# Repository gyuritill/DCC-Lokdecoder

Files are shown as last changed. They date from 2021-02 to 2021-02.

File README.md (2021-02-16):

# DCC-Lokdecoder
## Description
DCC multifunction decoder for H0 locomotives
## Features
- 1 motor H-bridge output
  - 3.6 A peak current
  - PWM frequency configurable (1-40 kHz)
  - overcurrent and temperature protected
- 10 function outputs
  - 115 mA per output
  - F0f, F0r, AUX1 and AUX2 are dimmable *todo*
  - mappable to F0-F12 function keys
- DCC asymmetry can be detected (for automatic brake control) *todo*
## Hardware
- 4-layer PCB esigned in KiCAD
- fairly standard components (available from Digi-Key, Farnell, Mouser, etc...)
- hand solderable (I did it too)
- 4 debug LEDs (red, yellow, green and blue)

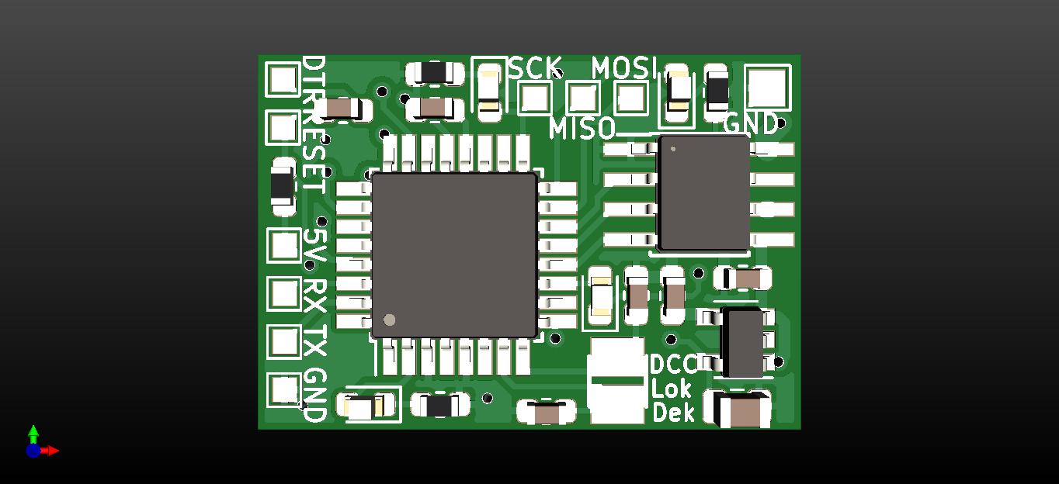
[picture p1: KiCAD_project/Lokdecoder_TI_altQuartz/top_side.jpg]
top
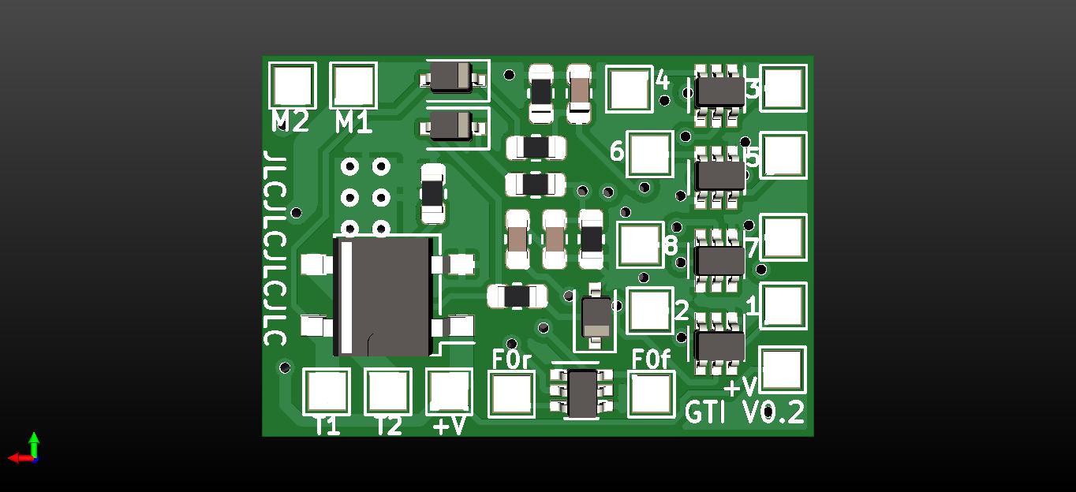
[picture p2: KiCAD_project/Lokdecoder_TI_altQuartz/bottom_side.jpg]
bottom
|  |  |
| :---: | :---: |
| top side | bottom side |

## Firmware
- Arduino compatible programming (behaves like an UNO)
- DCC decoding by [NmraDcc](https://github.com/mrrwa/NmraDcc) library

## JMRI integration

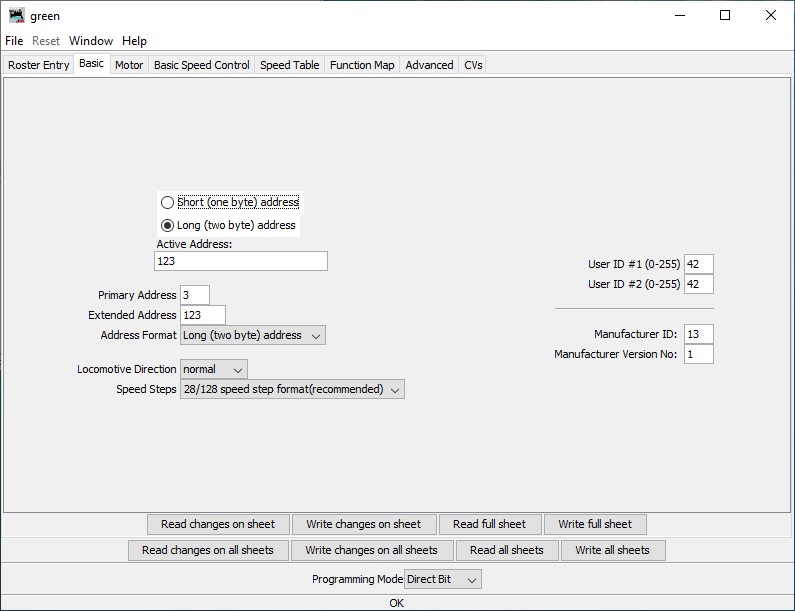
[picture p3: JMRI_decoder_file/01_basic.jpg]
basic
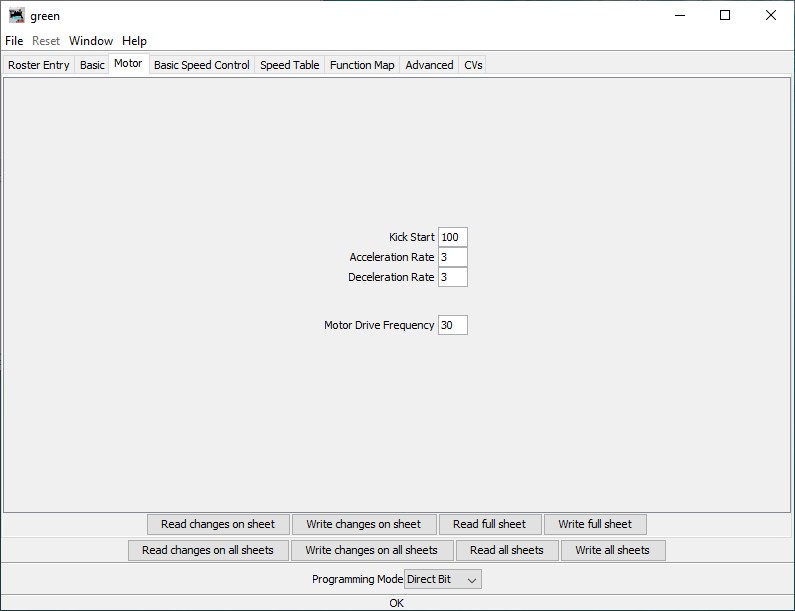
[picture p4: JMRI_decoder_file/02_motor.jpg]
motor
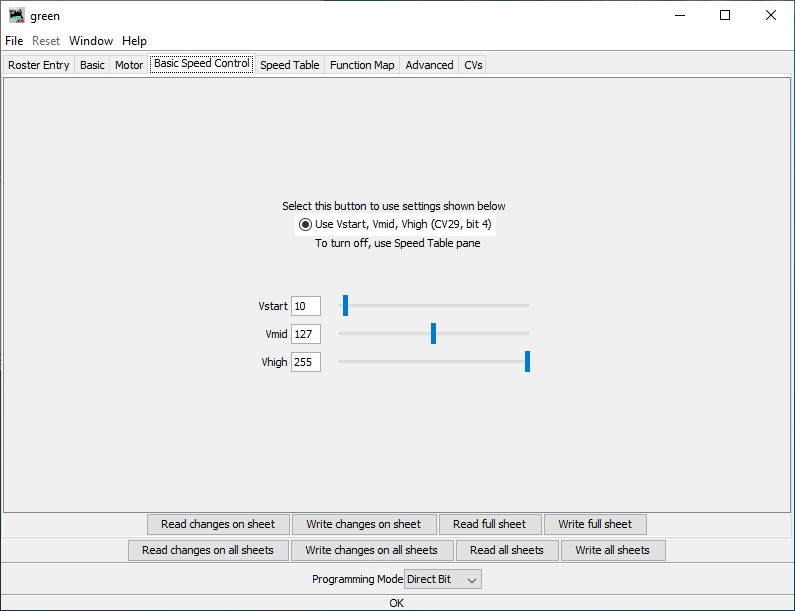
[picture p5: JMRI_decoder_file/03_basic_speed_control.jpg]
basic_speed
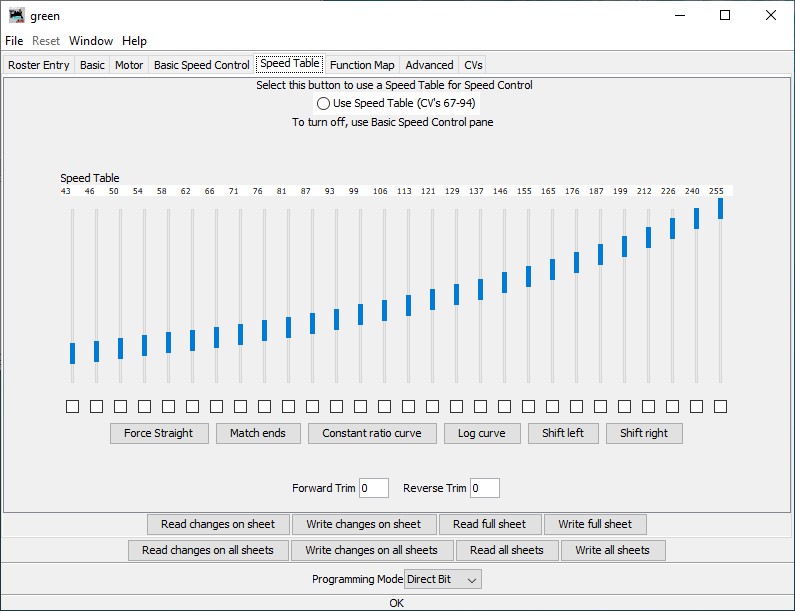
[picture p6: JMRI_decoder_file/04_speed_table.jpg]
speed_table
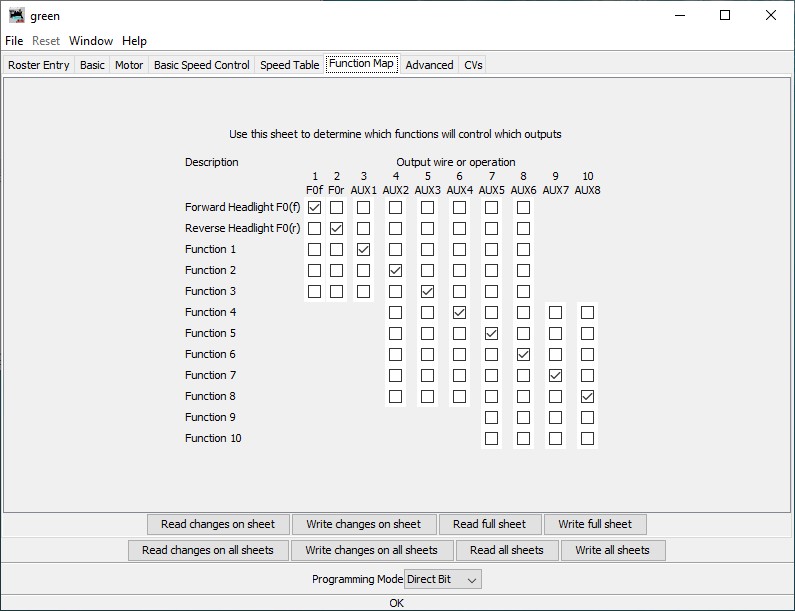
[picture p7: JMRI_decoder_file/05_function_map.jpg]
function_map
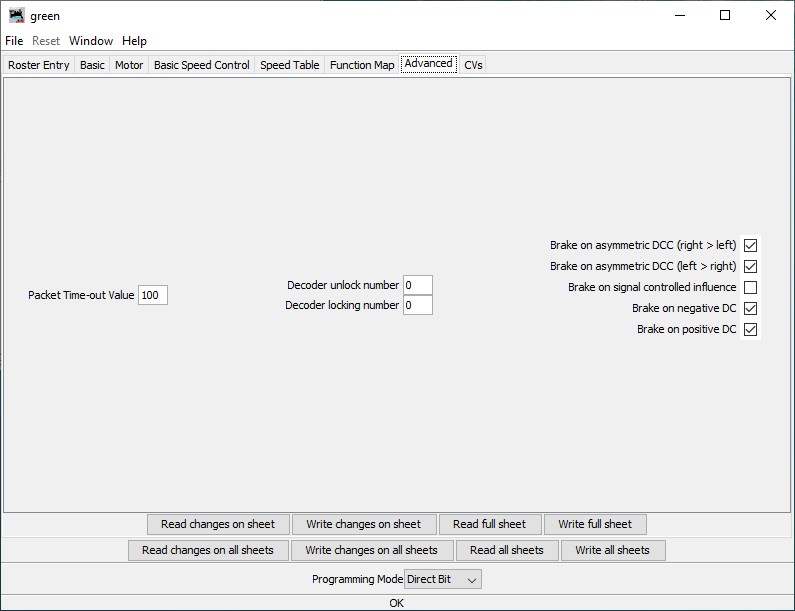
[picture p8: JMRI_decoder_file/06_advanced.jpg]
advanced
|  |  |  |  |  |  |
| :---: | :---: | :---: | :---: | :---: | :---: |
| Basic  | Motor | Basic speed control | Speed table | Function map | Advanced |

## Install guide

1. Get the PCB (e.g. [JLCPCB](https://jlcpcb.com/)) and the components (e.g. [mouser](https://www.mouser.at/), [digikey](https://www.digikey.at/))
2. Solder the components. The SOIC with exposed pad is a bit tricky, it can be soldered from the other side with a big tip and a lot of flux.
3. Install the Arduino bootloader using the pads 5V, GND, SCK, MISO, MOSI, RST and an Arduino. [Arduino as ISP](https://www.arduino.cc/en/Tutorial/BuiltInExamples/ArduinoISP)
4. Uncomment the line `#define RESET_FACTORY_DEFAULTS` to fill the EEPROM with the default CV values
5. Upload the code using the pads 5V, GND, RX, TX, DTR and a USB TTL UART cable [like this](https://www.mouser.at/ProductDetail/FTDI/TTL-232R-5V-WE/?qs=OMDV80DKjRpCUAS6UR9QpQ%3D%3D)
6. Re-comment the line `#define RESET_FACTORY_DEFAULTS` to avoid resetting to factory defaults every time.
7. Upload the code again.
8. Add the decoder XML file to JMRI. In DecoderPro select "File-> Import Decoder File..." and browse to the decoder [XML](JMRI_decoder_file/Public_Domain_GTI_green.xml). It will take some time, then adds the decoder definition to the database.
9. Connect the T1 and T2 pads to the programming track of your DCC system.
10. Add new locomotive with the "New Loco" button and then "Read type from decoder". It should detect the correct type:
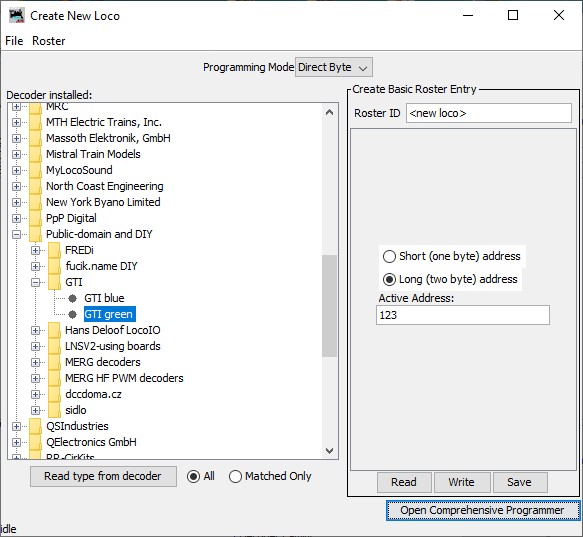
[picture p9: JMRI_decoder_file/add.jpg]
add

11. If everything is fine, you can install the decoder into your locomotive!
### Pinout
| Pad | Function |
| :-- | :-- |
| M1 | Motor 1 |
| M2 | Motor 2 |
| T1 | Track 1 |
| T2 | Track 2 |
| V+ | Positive common for function outputs (keep-alive capacitor positive) |
| F0f | F0 function output forward (open drain) |
| F0r | F0 function output reverse (open drain) |
| 1-8 | AUX function output n (open drain) |
| 5V | internal microcontroller +5V supply |
| GND | ground (keep alive capacitor negative) |
| SCK | ISP programming clock (connect to ISP SCK) |
| MISO | ISP programming read (connect to ISP MISO) |
| MOSI | ISP programming write (connect to ISP MOSI) |
| RST | ISP programming reset (connect to ISP reset output)
| RX | serial programming receive (connect to TTL UART TX) |
| TX | serial programming transmit (connect to TTL UART RX) |
| DTR | serial programming reset through a 100 nF capacitor (connect to TTL UART DTR) |

## Todo list
- [ ] CV15, CV16 decoder locking
- [ ] CV65 kick start
- [ ] CV67-94 speed table
- [ ] CV27 automatic brake control
- [ ] function output dimming
- [ ] motor fault check

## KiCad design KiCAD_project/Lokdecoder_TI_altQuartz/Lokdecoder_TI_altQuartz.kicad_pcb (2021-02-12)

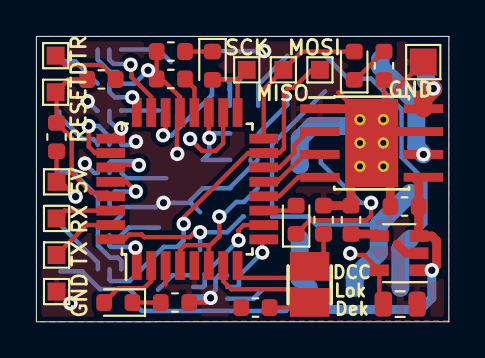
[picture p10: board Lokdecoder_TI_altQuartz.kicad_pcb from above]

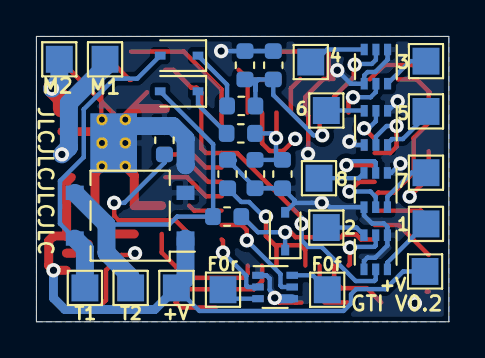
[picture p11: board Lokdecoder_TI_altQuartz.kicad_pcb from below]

Board: 4 copper layers, 22.9 x 15.8 mm, 63 parts (34 on the bottom side), 51 nets.

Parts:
C1, C2, C5, C10: 100nF; C_0603_1608Metric
C3: 470pF; C_0603_1608Metric
C4: 2.2uF; C_0805_2012Metric
C6, C7: 4.7uF; C_0603_1608Metric
C8, C9: 10pF; C_0603_1608Metric
D1: D_Bridge_+-AA; TO-269AA
D2: MM3Z4V7ST1G; D_SOD-323
D3, D4: NSR0530HT1G; D_SOD-323
D5: Ye_LED; LED_0603_1608Metric
D6: Gr_LED; LED_0603_1608Metric
D7: Rd_LED; LED_0603_1608Metric
D8: Bl_LED; LED_0603_1608Metric
IC1: MIC5205-5.0YM5-TR; SOT-23-5
IC2: ATMEGA328P-AUR; TQFP-32_7x7mm_P0.8mm
IC3: DRV8872DDAR; Texas_HTSOP-8-1EP_3.9x4.9mm_P1.27mm_EP2.95x4.9mm_Mask2.4x3.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
R1, R5, R6: 4.7k; R_0603_1608Metric
R2, R3, R4: 27k; R_0603_1608Metric
R7, R9, R10, R11: 1k; R_0603_1608Metric
T1, T2, T3, T4, T5: 2N7002DWCT; SOT-363_SC-70-6
TP1: M1; TestPoint_Pad_1.5x1.5mm
TP2: M2; TestPoint_Pad_1.5x1.5mm
TP3: T1; TestPoint_Pad_1.5x1.5mm
TP4: T2; TestPoint_Pad_1.5x1.5mm
TP5: GND; TestPoint_Pad_1.5x1.5mm
TP6, TP17: +V; TestPoint_Pad_1.5x1.5mm
TP7: F0f; TestPoint_Pad_1.5x1.5mm
TP8: F0r; TestPoint_Pad_1.5x1.5mm
TP9: 1; TestPoint_Pad_1.5x1.5mm
TP10: 2; TestPoint_Pad_1.5x1.5mm
TP11: 3; TestPoint_Pad_1.5x1.5mm
TP12: 4; TestPoint_Pad_1.5x1.5mm
TP13: 5; TestPoint_Pad_1.5x1.5mm
TP14: 6; TestPoint_Pad_1.5x1.5mm
TP15: 7; TestPoint_Pad_1.5x1.5mm
TP16: 8; TestPoint_Pad_1.5x1.5mm
TP18: RESET; TestPoint_Pad_1.0x1.0mm
TP19: SCK; TestPoint_Pad_1.0x1.0mm
TP20: MISO; TestPoint_Pad_1.0x1.0mm
TP21: MOSI; TestPoint_Pad_1.0x1.0mm
TP22: 5V; TestPoint_Pad_1.0x1.0mm
TP23: RX; TestPoint_Pad_1.0x1.0mm
TP24: TX; TestPoint_Pad_1.0x1.0mm
TP25: DTR; TestPoint_Pad_1.0x1.0mm
TP26: GND; TestPoint_Pad_1.0x1.0mm
X1: 16M; Crystal_SMD_2520-2Pin_2.5x2.0mm_HandSoldering

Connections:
+5V: C4.1, C5.2, IC1.5, IC2.4, IC2.6, IC2.18, R1.2, TP22.1
/A0: IC2.23, T4.2
/A1: IC2.24, T4.5
/A2: IC2.25, T5.2
/A3: IC2.26, T5.5
/A4: IC2.27, T3.2
/A5: IC2.28, T3.5
/A6: C6.2, IC2.19, R3.1, R5.1
/A7: C7.2, IC2.22, R4.1, R6.1
/AUX1: T2.6, TP9.1
/AUX1_TTL: IC2.1, T2.2
/AUX2: T2.3, TP10.1
/AUX2_TTL: IC2.15, T2.5, TP21.1
/AUX3: T4.6, TP11.1
/AUX4: T4.3, TP12.1
/AUX5: T5.6, TP13.1
/AUX6: T5.3, TP14.1
/AUX7: T3.6, TP15.1
/AUX8: T3.3, TP16.1
/D0: IC2.30, TP23.1
/D1: IC2.31, TP24.1
/D2: D2.1, IC2.32, R2.1
/D4: D8.2, IC2.2
/D5: IC2.9, T1.2
/D6: IC2.10, T1.5
/D7: D7.2, IC2.11
/D8: IC2.12, IC3.4
/D9: IC2.13, IC3.3
/D10: IC2.14, IC3.2
/D12: D6.2, IC2.16, TP20.1
/D13: D5.2, IC2.17, TP19.1
/DCC1: D1.4, D4.2, TP3.1
/DCC2: D1.3, D3.2, R2.2, TP4.1
/DTR: C1.2, TP25.1
/F0f: T1.6, TP7.1
/F0r: T1.3, TP8.1
/MOT1: IC3.6, TP1.1
/MOT2: IC3.8, TP2.1
/RESET: C1.1, IC2.29, R1.1, TP18.1
GND: C2.2, C3.1, C4.2, C5.1, C6.1, C7.1, C8.1, C9.1, C10.1, D1.2, D2.2, IC1.2, IC2.3, IC2.5, IC2.21, IC3.1, IC3.7, IC3.9, R5.2, R6.2, R7.1, R9.1, R10.1, R11.1, T1.1, T1.4, T2.1, T2.4, T3.1, T3.4, T4.1, T4.4, T5.1, T5.4, TP5.1, TP26.1
unnamed: C2.1, IC2.20
unnamed: C3.2, IC1.4
unnamed: C8.2, IC2.7, X1.1
unnamed: C9.2, IC2.8, X1.2
unnamed: D3.1, R3.2
unnamed: D4.1, R4.2
unnamed: D5.1, R9.2
unnamed: D6.1, R10.2
unnamed: D7.1, R11.2
unnamed: D8.1, R7.2
VCC: C10.2, D1.1, IC1.1, IC1.3, IC3.5, TP6.1, TP17.1

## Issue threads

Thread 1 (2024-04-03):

Questions about setting a high PWM frequency and motor drive handling

murarduino, 2024-04-03:
Dear gyuritill,

I noticed that in your project, the motor driver component is selected from the Ti company DRV8872. This is a typical SOP-8 motor driver chip. I checked the datasheet for DRV8872. In the Fpwm Recommended Operating Conditions has a line in the note:
The voltages applied to the inputs should have at least 800 ns of pulse width to ensure detection. Typical devices require at least 400 ns. If the PWM frequency is 200 kHz, the usable duty cycle range is 16% to 84%

I think this is because it has to do with the motor drive internal MOSFET switching time and the time spent in logic processing. Although only the tDEAD time is listed in the Electrical Characteristics table, this issue is described in 7.3.4 Dead Time.

I understand that this is the minimum duration of a PWM square wave (high level). or that PWM square wave need to be greater than (at least equal to) this time.

In the decoder, the PWM resolution is usually set to 2^8. 256。 The minimum duty cycle needs to be greater than this time
Take the decoder PWM frequency set to 40KHz for example. The PWM cycle time is 25us, and dividing by 256 (1/256) is almost 100ns. According to the note, it is necessary to set the duty cycle to 8 in Vstart (to be equal to 8 in step1 of the Speed Table). Am I right to interpret it this way?
Similarly, in high frequency PWM settings, special attention needs to be paid to the duty cycle value of step1.

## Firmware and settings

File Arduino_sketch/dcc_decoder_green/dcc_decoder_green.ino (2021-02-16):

// for ATMEGA328P
#include <NmraDcc.h>

// Uncomment to force CV Reset to Factory Defaults
//#define RESET_FACTORY_DEFAULTS

// Uncomment any of the lines below to enable debug messages for different parts of the code
//#define DEBUG_DCC_MSG

#if defined(DEBUG_FUNCTIONS) or defined(DEBUG_SPEED) or defined(DEBUG_PWM) or defined(DEBUG_DCC_ACK) or defined(DEBUG_DCC_MSG) or defined(DEBUG_STATE)
#define DEBUG_PRINT
#endif

#define DECODER_ADDRESS 3
#define LONG_ADDRESS 123

#define CV_VSTART 2
#define START_VOLTAGE 10 // 255 is full rectified voltage

#define CV_ACC_RATE 3
#define ACC_RATE 3 // value*0.896/speed_steps sec/step 3->2.688 sec to full speed

#define CV_DEC_RATE 4
#define DEC_RATE 3 // value*0.896/speed_steps sec/step 3->2.688 sec from full speed

#define CV_VHIGH 5
#define HIGH_VOLTAGE 255 // 255 is full rectified voltage

#define CV_VMID 6
#define MID_VOLTAGE 127 // 255 is full rectified voltage

#define VERSION 1           // CV 7

#define CV_PWM_PERIOD 9
#define PWM_PERIOD 1

#define CV_PACKET_TIMEOUT 11
#define PACKET_TIMEOUT 100 // x 10ms
#define CV_UNLOCK_NUMBER 15
#define CV_LOCKING_NUMBER 16
#define CV_AUTO_STOP_CONFIG 27
#define CV_OUTPUT_LOCATION_F0f 33
#define CV_OUTPUT_LOCATION_F0r 34
#define CV_OUTPUT_LOCATION_F1 35
#define CV_OUTPUT_LOCATION_F2 36
#define CV_OUTPUT_LOCATION_F3 37
#define CV_OUTPUT_LOCATION_F4 38
#define CV_OUTPUT_LOCATION_F5 39
#define CV_OUTPUT_LOCATION_F6 40
#define CV_OUTPUT_LOCATION_F7 41
#define CV_OUTPUT_LOCATION_F8 42
#define CV_OUTPUT_LOCATION_F9 43
#define CV_OUTPUT_LOCATION_F10 44
#define CV_OUTPUT_LOCATION_F11 45
#define CV_OUTPUT_LOCATION_F12 46
#define CV_PRODUCT_ID 47  //Product ID: 47-50 (CV47<<24 + CV48<<16 + CV49<<8 + CV50)
#define CV_KICK_START 65
#define CV_FWD_TRIM 66
#define CV_SPEED_MAP 67 //67-94
#define CV_REV_TRIM 95
#define CV_USER_ID1 105
#define CV_USER_ID2 106

//todo
// function effects 57-61, dimming, inverting, 0-speed activate/deactivate
// SW_IN function mapping, minimum time
// overload amplitude, time

#define DCC_PIN       2
#define MOTOR_IN1_PIN 9
#define MOTOR_IN2_PIN 10
#define MOTOR_nFAULT_PIN 8
#define LED_F0f_PIN   5
#define LED_F0r_PIN   6
#define LED_AUX1_PIN  3
#define LED_AUX2_PIN  11
#define LED_AUX3_PIN  A0
#define LED_AUX4_PIN  A1
#define LED_AUX5_PIN  A2
#define LED_AUX6_PIN  A3
#define LED_AUX7_PIN  A4
#define LED_AUX8_PIN  A5
#define LED_GREEN_PIN 12
#define LED_YELLOW_PIN 13
#define LED_RED_PIN    7
#define LED_BLUE_PIN   4
#define DCC1_PK_PIN   A6
#define DCC2_PK_PIN   A7

NmraDcc dcc;

struct CVPair{
  uint16_t CV;
  uint8_t  Value;
};

CVPair factoryDefaultCVs [] =
{
  {CV_MULTIFUNCTION_PRIMARY_ADDRESS, DECODER_ADDRESS&0x7F },//CV1
  {CV_VSTART, START_VOLTAGE },//CV2
  {CV_ACC_RATE, ACC_RATE },//CV3
  {CV_DEC_RATE, DEC_RATE },//CV4
  {CV_VHIGH, HIGH_VOLTAGE },//CV5
  {CV_VMID, MID_VOLTAGE },//CV6, (CV7, CV8 implicit in dcc.init())
  {CV_PWM_PERIOD, PWM_PERIOD},//CV9
  {CV_PACKET_TIMEOUT, PACKET_TIMEOUT},//CV11
  {CV_UNLOCK_NUMBER, 0},//CV15
  {CV_LOCKING_NUMBER, 0},//CV16
  {CV_MULTIFUNCTION_EXTENDED_ADDRESS_MSB, highByte(LONG_ADDRESS) + 0xC0}, //CV17
  {CV_MULTIFUNCTION_EXTENDED_ADDRESS_LSB, lowByte(LONG_ADDRESS)},         //CV18
  {CV_AUTO_STOP_CONFIG, 0b00110011},//CV27 7,6: reserved, 5: DC+, 4: DC-, 3: unused, 2: Signal, 1: Asym left, 0: Asym right
  {CV_29_CONFIG, 0x00
  //| CV29_LOCO_DIR            // 0: normal direction, 1: reversed direction
  | CV29_F0_LOCATION           // 0: 14 speed steps, 1:28/128 speed steps
  //| CV29_APS                 // 0: only DCC, 1: analogue enabled
  //| CV29_ADV_ACK             // 0: Railcom disabled, 1: Railcom enabled
  //| CV29_SPEED_TABLE_ENABLE  // 0: simple speed curve (CV2, CV5, CV6)
#ifdef LONG_ADDRESS
  | CV29_EXT_ADDRESSING        // 0: one byte addressing, 1: two byte addressing
#endif
  //| CV29_OUTPUT_ADDRESS_MODE // 0: Decoder Address Mode, 1: Output Address Mode
  //| CV29_ACCESSORY_DECODER   // 0: Multi-Function Decoder Mode, 1: Accessory Decoder Mode
  },
  //CVs33-46
  {CV_OUTPUT_LOCATION_F0f, 1},// 1:F0f, 2:F0r, 4:AUX1, 8:AUX2, 16:AUX3, 32:AUX4, 64:AUX5, 128:AUX6
  {CV_OUTPUT_LOCATION_F0r, 2},// 1:F0f, 2:F0r, 4:AUX1, 8:AUX2, 16:AUX3, 32:AUX4, 64:AUX5, 128:AUX6
  {CV_OUTPUT_LOCATION_F1, 4}, // 1:F0f, 2:F0r, 4:AUX1, 8:AUX2, 16:AUX3, 32:AUX4, 64:AUX5, 128:AUX6
  {CV_OUTPUT_LOCATION_F2, 8}, // 1:F0f, 2:F0r, 4:AUX1, 8:AUX2, 16:AUX3, 32:AUX4, 64:AUX5, 128:AUX6
  {CV_OUTPUT_LOCATION_F3, 16},// 1:F0f, 2:F0r, 4:AUX1, 8:AUX2, 16:AUX3, 32:AUX4, 64:AUX5, 128:AUX6
  {CV_OUTPUT_LOCATION_F4, 4}, // 1:AUX2, 2:AUX3, 4:AUX4, 8:AUX5, 16:AUX6, 32:AUX7, 64:AUX8
  {CV_OUTPUT_LOCATION_F5, 8}, // 1:AUX2, 2:AUX3, 4:AUX4, 8:AUX5, 16:AUX6, 32:AUX7, 64:AUX8
  {CV_OUTPUT_LOCATION_F6, 16},// 1:AUX2, 2:AUX3, 4:AUX4, 8:AUX5, 16:AUX6, 32:AUX7, 64:AUX8
  {CV_OUTPUT_LOCATION_F7, 32},// 1:AUX2, 2:AUX3, 4:AUX4, 8:AUX5, 16:AUX6, 32:AUX7, 64:AUX8
  {CV_OUTPUT_LOCATION_F8, 64},// 1:AUX2, 2:AUX3, 4:AUX4, 8:AUX5, 16:AUX6, 32:AUX7, 64:AUX8
  {CV_OUTPUT_LOCATION_F9, 0}, // 1:AUX5, 2:AUX6, 4:AUX7, 8:AUX8
  {CV_OUTPUT_LOCATION_F10, 0},// 1:AUX5, 2:AUX6, 4:AUX7, 8:AUX8
  {CV_OUTPUT_LOCATION_F11, 0},// 1:AUX5, 2:AUX6, 4:AUX7, 8:AUX8
  {CV_OUTPUT_LOCATION_F12, 0},// 1:AUX5, 2:AUX6, 4:AUX7, 8:AUX8
  {CV_PRODUCT_ID+0, 0},  // CV47 product ID highest byte
  {CV_PRODUCT_ID+1, 0},  // CV48 product ID high byte
  {CV_PRODUCT_ID+2, 1},  // CV49 product ID low byte
  {CV_PRODUCT_ID+3, 2},  // CV50 product ID lowest byte
  {CV_KICK_START, 100},  // CV65
  {CV_FWD_TRIM, 128},    // CV66
  //CVs 67-94
  {CV_SPEED_MAP+0, 43},
  {CV_SPEED_MAP+1, 46},
  {CV_SPEED_MAP+2, 50},
  {CV_SPEED_MAP+3, 54},
  {CV_SPEED_MAP+4, 58},
  {CV_SPEED_MAP+5, 62},
  {CV_SPEED_MAP+6, 66},
  {CV_SPEED_MAP+7, 71},
  {CV_SPEED_MAP+8, 76},
  {CV_SPEED_MAP+9, 81},
  {CV_SPEED_MAP+10, 87},
  {CV_SPEED_MAP+11, 93},
  {CV_SPEED_MAP+12, 99},
  {CV_SPEED_MAP+13, 106},
  {CV_SPEED_MAP+14, 113},
  {CV_SPEED_MAP+15, 121},
  {CV_SPEED_MAP+16, 129},
  {CV_SPEED_MAP+17, 137},
  {CV_SPEED_MAP+18, 146},
  {CV_SPEED_MAP+19, 155},
  {CV_SPEED_MAP+20, 165},
  {CV_SPEED_MAP+21, 176},
  {CV_SPEED_MAP+22, 187},
  {CV_SPEED_MAP+23, 199},
  {CV_SPEED_MAP+24, 212},
  {CV_SPEED_MAP+25, 226},
  {CV_SPEED_MAP+26, 240},
  {CV_SPEED_MAP+27, 255},
  {CV_REV_TRIM, 128}, //CV95
  {CV_USER_ID1, 42},  //CV105
  {CV_USER_ID2, 42},  //CV106
};

uint8_t factoryDefaultCVIndex = 0;
// state variables
uint8_t numSpeedSteps = SPEED_STEP_128;
uint32_t lastFunctionState;
uint32_t newFunctionState;
uint16_t lastOutputState = 0;
uint16_t newOutputState = 0;
bool lastDirection;   // DCC_DIR_FWD(1): (a+/b-), DCC_DIR_REV(0): rev (a-/b+)
bool newDirection;    // DCC_DIR_FWD(1): (a+/b-), DCC_DIR_REV(0): rev (a-/b+)
bool actualDirection; // DCC_DIR_FWD(1): (a+/b-), DCC_DIR_REV(0): rev (a-/b+)
uint8_t lastSpeed;    // 0-127, 0:EMCY stop, 1: normal stop, 2-127: drive
uint8_t newSpeed;     // 0-127, 0:EMCY stop, 1: normal stop, 2-127: drive
uint8_t actualSpeed;
uint8_t targetSpeed;
uint8_t savedSpeed;
// timing for acceleration / deceleration
uint32_t lastSpeedStep = 0;
uint32_t newSpeedStep = 0;
// timeout
uint32_t packetTimeout;
uint32_t lastPacket;
// configuration variables
uint8_t vStart;
uint8_t vMid;
uint8_t vHigh;
uint8_t accRate;
uint8_t decRate;
uint8_t pwmFreq;
uint8_t fwdTrim;
uint8_t revTrim;
uint8_t kickStart;
uint8_t functionMapping[14];
uint16_t maxOCR;
uint8_t speedTable[28];
uint8_t autoStop;
uint8_t unlockNumber;
uint8_t lockingNumber;

void notifyCVResetFactoryDefault(){
/*+
 *  notifyCVResetFactoryDefault() Called when CVs must be reset.
 *                                This is called when CVs must be reset
 *                                to their factory defaults. This callback
 *                                should write the factory default value of
 *                                relevent CVs using the setCV() method.
 *                                setCV() must not block whens this is called.
 *                                Test with isSetCVReady() prior to calling setCV()
 *
 *  Inputs:
 *    None
 *                                                                                                        *
 *  Returns:
 *    None
 */
// Make FactoryDefaultCVIndex non-zero and equal to num CV's to be reset 
// to flag to the loop() function that a reset to Factory Defaults needs to be done
  factoryDefaultCVIndex = sizeof(factoryDefaultCVs)/sizeof(CVPair);
};

void notifyDccReset(uint8_t hardReset){
/*+
 *  notifyDccReset(uint8_t hardReset) Callback for a DCC reset command.
 *
 *  Inputs:
 *    hardReset - 0 normal reset command.
 *                1 hard reset command.
 *
 *  Returns:
 *    None
 */
  ;
}

void notifyDccIdle(void){
/*+
 *  notifyDccIdle() Callback for a DCC idle command.
 *
 *  Inputs:
 *    None
 *
 *  Returns:
 *    None
 */
  ;
}

void notifyCVChange( uint16_t CV, uint8_t Value){
/*+
 *  notifyCVChange()  Called when a CV value is changed.
 *                    This is called whenever a CV's value is changed.
 *  notifyDccCVChange()  Called only when a CV value is changed by a Dcc packet or a internal lib function.
 *                    it is NOT called if the CV is changed by means of the setCV() method.
 *                    Note: It is not called if notifyCVWrite() is defined
 *                    or if the value in the EEPROM is the same as the value
 *                    in the write command. 
 *
 *  Inputs:
 *    CV        - CV number.
 *    Value     - Value of the CV.
 *
 *  Returns:
 *    None
 */
  switch(CV){
    case CV_VSTART:
      vStart = Value;
      break;
    case CV_ACC_RATE:
      accRate = Value;
      break;
    case CV_DEC_RATE:
      decRate = Value;
      break;
    case CV_VMID:
      vMid = Value;
      break;
    case CV_VHIGH:
      vHigh = Value;
      break;
    case CV_PWM_PERIOD:
      pwmFreq = Value;
      break;
    case CV_OUTPUT_LOCATION_F0f:
    case CV_OUTPUT_LOCATION_F0r:
    case CV_OUTPUT_LOCATION_F1:
    case CV_OUTPUT_LOCATION_F2:
    case CV_OUTPUT_LOCATION_F3:
    case CV_OUTPUT_LOCATION_F4:
    case CV_OUTPUT_LOCATION_F5:
    case CV_OUTPUT_LOCATION_F6:
    case CV_OUTPUT_LOCATION_F7:
    case CV_OUTPUT_LOCATION_F8:
    case CV_OUTPUT_LOCATION_F9:
    case CV_OUTPUT_LOCATION_F10:
    case CV_OUTPUT_LOCATION_F11:
    case CV_OUTPUT_LOCATION_F12:
      functionMapping[CV - CV_OUTPUT_LOCATION_F0f] = Value;
      break;
    case CV_PACKET_TIMEOUT:
      packetTimeout = 10 * Value;
      break;
    case CV_FWD_TRIM:
      fwdTrim = Value;
      break;
    case CV_REV_TRIM:
      revTrim = Value;
      break;
    case CV_KICK_START:
      kickStart = Value;
      break;
    case CV_AUTO_STOP_CONFIG:
      autoStop = Value;
      break;
    case CV_UNLOCK_NUMBER:
      unlockNumber = Value;
      break;
    case CV_LOCKING_NUMBER:
      lockingNumber = Value;
      break;
  }
  if((CV >= CV_SPEED_MAP) && (CV <= (CV_SPEED_MAP+27))){
    speedTable[CV - CV_SPEED_MAP] = Value;
  }
}

void notifyDccSpeed(uint16_t Addr, DCC_ADDR_TYPE AddrType, uint8_t Speed, DCC_DIRECTION Dir, DCC_SPEED_STEPS SpeedSteps){
/*+
 *  notifyDccSpeed() Callback for a multifunction decoder speed command.
 *                   The received speed and direction are unpacked to separate values.
 *
 *  Inputs:
 *    Addr        - Active decoder address.
 *    AddrType    - DCC_ADDR_SHORT or DCC_ADDR_LONG.
 *    Speed       - Decoder speed. 0               = Emergency stop
 *                                 1               = Regular stop
 *                                 2 to SpeedSteps = Speed step 1 to max.
 *    Dir         - DCC_DIR_REV or DCC_DIR_FWD
 *    SpeedSteps  - Highest speed, SPEED_STEP_14   =  15
 *                                 SPEED_STEP_28   =  29
 *                                 SPEED_STEP_128  = 127
 *
 *  Returns:
 *    None
 */
  newDirection = Dir;
  newSpeed = Speed;
  numSpeedSteps = SpeedSteps;
}

void notifyDccFunc(uint16_t Addr, DCC_ADDR_TYPE AddrType, FN_GROUP FuncGrp, uint8_t FuncState){
/*+
 *  notifyDccFunc() Callback for a multifunction decoder function command.
 *
 *  Inputs:
 *    Addr        - Active decoder address.
 *    AddrType    - DCC_ADDR_SHORT or DCC_ADDR_LONG.
 *    FuncGrp     - Function group. FN_0      - 14 speed step headlight function.
 *                                                                  Mask FN_BIT_00.
 *                                  FN_0_4    - Functions  0 to  4. Mask FN_BIT_00 - FN_BIT_04
 *                                  FN_5_8    - Functions  5 to  8. Mask FN_BIT_05 - FN_BIT_08
 *                                  FN_9_12   - Functions  9 to 12. Mask FN_BIT_09 - FN_BIT_12
 *                                  FN_13_20  - Functions 13 to 20. Mask FN_BIT_13 - FN_BIT_20 
 *                                  FN_21_28  - Functions 21 to 28. Mask FN_BIT_21 - FN_BIT_28
 *    FuncState   - Function state. Bitmask where active functions have a 1 at that bit.
 *                                  You must & FuncState with the appropriate
 *                                  FN_BIT_nn value to isolate a given bit.
 *
 *  Returns:
 *    None
 */
  switch(FuncGrp){
    case FN_0_4:
      bitWrite(newFunctionState, 0, FuncState & FN_BIT_00);
      bitWrite(newFunctionState, 1, FuncState & FN_BIT_01);
      bitWrite(newFunctionState, 2, FuncState & FN_BIT_02);
      bitWrite(newFunctionState, 3, FuncState & FN_BIT_03);
      bitWrite(newFunctionState, 4, FuncState & FN_BIT_04);
      break;
    case FN_5_8:
      bitWrite(newFunctionState, 5, FuncState & FN_BIT_05);
      bitWrite(newFunctionState, 6, FuncState & FN_BIT_06);
      bitWrite(newFunctionState, 7, FuncState & FN_BIT_07);
      bitWrite(newFunctionState, 8, FuncState & FN_BIT_08);
      break;
    case FN_9_12:
      bitWrite(newFunctionState, 9, FuncState & FN_BIT_09);
      bitWrite(newFunctionState, 10, FuncState & FN_BIT_10);
      bitWrite(newFunctionState, 11, FuncState & FN_BIT_11);
      bitWrite(newFunctionState, 12, FuncState & FN_BIT_12);
      break;
    case FN_13_20:
      bitWrite(newFunctionState, 13, FuncState & FN_BIT_13);
      bitWrite(newFunctionState, 14, FuncState & FN_BIT_14);
      bitWrite(newFunctionState, 15, FuncState & FN_BIT_15);
      bitWrite(newFunctionState, 16, FuncState & FN_BIT_16);
      bitWrite(newFunctionState, 17, FuncState & FN_BIT_17);
      bitWrite(newFunctionState, 18, FuncState & FN_BIT_18);
      bitWrite(newFunctionState, 19, FuncState & FN_BIT_19);
      bitWrite(newFunctionState, 20, FuncState & FN_BIT_20);
      break;
    case FN_21_28:
      bitWrite(newFunctionState, 21, FuncState & FN_BIT_21);
      bitWrite(newFunctionState, 22, FuncState & FN_BIT_22);
      bitWrite(newFunctionState, 23, FuncState & FN_BIT_23);
      bitWrite(newFunctionState, 24, FuncState & FN_BIT_24);
      bitWrite(newFunctionState, 25, FuncState & FN_BIT_25);
      bitWrite(newFunctionState, 26, FuncState & FN_BIT_26);
      bitWrite(newFunctionState, 27, FuncState & FN_BIT_27);
      bitWrite(newFunctionState, 28, FuncState & FN_BIT_28);
      break;
  }
}

#ifdef  DEBUG_DCC_MSG
void notifyDccMsg( DCC_MSG * Msg){
/*+
 *  notifyDccMsg() Raw DCC packet callback.
 *                 Called with raw DCC packet bytes.
 *
 *  Inputs:
 *    Msg        - Pointer to DCC_MSG structure. The values are:
 *                 Msg->Size          - Number of Data bytes in the packet.
 *                 Msg->PreambleBits  - Number of preamble bits in the packet.
 *                 Msg->Data[]        - Array of data bytes in the packet.
 *
 *  Returns:
 *    None
 */
  Serial.print("notifyDccMsg: ") ;
  for(uint8_t i = 0; i < Msg->Size; i++){
    Serial.print(Msg->Data[i], HEX);
    Serial.write(' ');
  }
  Serial.println();
}
#endif

void notifyCVAck(void){
/*+
 *  notifyCVAck() Called when a CV write must be acknowledged.
 *                This callback must increase the current drawn by this
 *                decoder by at least 60mA for 6ms +/- 1ms.
 *
 *  Inputs:
 *    None
 *                                                                                                        *
 *  Returns:
 *    None
 */
  static bool ackDir = false;
  OCR1A = ackDir ? maxOCR : 0;
  OCR1B = ackDir ? 0 : maxOCR;
  delay(6);
  OCR1A = 0;
  OCR1B = 0;
  ackDir = !ackDir;
}
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
void loop(){
  if(dcc.process()){        // update last valid packet reception time
    lastPacket = millis();
  }
  if((millis()-lastPacket) > packetTimeout){  // timeout since last valid packet
    newSpeed = 0;
  }
  switch(dcc.getDccPolarity()){
    case RISING:
      digitalWrite(LED_GREEN_PIN, LOW);
      digitalWrite(LED_BLUE_PIN, HIGH);
      break;
    case FALLING:
      digitalWrite(LED_GREEN_PIN, HIGH);
      digitalWrite(LED_BLUE_PIN, LOW);
      break;
  }
  // handle direction changes
  if(newDirection != actualDirection){
    if(lastDirection != newDirection){
      savedSpeed = targetSpeed;
      lastDirection = newDirection;
    }
    targetSpeed = 0;
    if(actualSpeed == 0){
      actualDirection = newDirection;
      targetSpeed = savedSpeed;
    }
  }else{
    targetSpeed = savedSpeed;
  }
  digitalWrite(LED_YELLOW_PIN, (actualDirection == DCC_DIR_FWD) || (newDirection == DCC_DIR_FWD));
  digitalWrite(LED_RED_PIN, (actualDirection == DCC_DIR_REV) || (newDirection == DCC_DIR_REV));
  // handle speed change
  if(lastSpeed != newSpeed){
    lastSpeed = newSpeed;
    if(newSpeed == 0){                    // Stop if speed = 0
      targetSpeed = actualSpeed = 0;
      OCR1A = 0;
      OCR1B = 0;
    }else if(newSpeed == 1){              // Stop if speed = 1
      targetSpeed = 0;
    }else{                                // Calculate PWM value in the range 1..255   
      uint8_t vScF1;                      // start to mid
      uint8_t vScF2;                      // mid to high
      uint8_t modSpeed = newSpeed - 1;    // 1-126
      uint8_t modSteps = numSpeedSteps - 1; // 14/28/126
      
      if((vHigh > 1) && (vHigh > vStart)){  // vHigh is valid
        if((vMid > 1) && (vHigh > vMid)){     // vMid is valid too, using vStart, vMid and vHigh
          vScF1 = vMid - vStart;
          vScF2 = vHigh - vMid;
        }else{                              // vMid invalid, using vStart and vHigh
          vScF2 = vScF1 = (vHigh - vStart)/2;
        }
      }else{                                // vHigh invalid, using only vStart
        vScF2 = vScF1 = (255 - vStart)/2;
      }

      if(modSpeed<modSteps/2){
        targetSpeed = (int16_t) vStart + 2*modSpeed*vScF1/modSteps;
      }else{
        targetSpeed = (int16_t) vStart + 2*modSpeed*vScF2/modSteps + vScF1 - vScF2;
      }
    }
    savedSpeed = targetSpeed;
  }
  
  // ramp up/down PWM
  if(targetSpeed != actualSpeed){
    newSpeedStep = millis();
    if(targetSpeed > actualSpeed){   // accelerating
      if((newSpeedStep - lastSpeedStep) > accRate*896/(numSpeedSteps-1)){
        lastSpeedStep = newSpeedStep;
        actualSpeed++;
      }
    }else{                  // decelerating
      if((newSpeedStep - lastSpeedStep) > decRate*896/(numSpeedSteps-1)){
        lastSpeedStep = newSpeedStep;
        actualSpeed--;
      }
    }
    if(actualDirection == DCC_DIR_FWD){    // DCC FWD
      OCR1B = 0;
      if(fwdTrim == 0){
        OCR1A = (uint32_t)actualSpeed * (uint32_t)maxOCR / 255UL;
      }else{
        OCR1A = (uint32_t)actualSpeed * (uint32_t)maxOCR / 255UL * (uint32_t)fwdTrim / 128UL;
      }
    }else{                // DCC REV
      OCR1A = 0;
      if(fwdTrim == 0){
        OCR1B = (uint32_t)actualSpeed * (uint32_t)maxOCR / 255UL;
      }else{
        OCR1B = (uint32_t)actualSpeed * (uint32_t)maxOCR / 255UL * (uint32_t)revTrim / 128UL;
      }
    }
    
  }
  
  if((newFunctionState != lastFunctionState)||(actualSpeed == 0)){  // handle function change, map to outputs
    lastFunctionState = newFunctionState;
    newOutputState = 0;
    if(actualDirection){        // F0f
      newOutputState |= (bitRead(newFunctionState, 0) ? functionMapping[0] : 0);
    }else{                    // F0r
      newOutputState |= (bitRead(newFunctionState, 0) ? functionMapping[1] : 0);
    }
    for(byte i=1;i<=3;i++){  //F1-F3
      newOutputState |= (bitRead(newFunctionState, i) ? functionMapping[i+1] : 0);
    }
    for(byte i=4;i<=8;i++){  //F4-F8
      newOutputState |= (bitRead(newFunctionState, i) ? functionMapping[i+1]<<3 : 0);
    }
    for(byte i=9;i<=12;i++){  //F9-F12
      newOutputState |= (bitRead(newFunctionState, i) ? functionMapping[i+1]<<6 : 0);
    }
  }

  if(newOutputState != lastOutputState){  // actualise outputs
    lastOutputState = newOutputState;
    digitalWrite(LED_F0f_PIN, bitRead(newOutputState, 0));
    digitalWrite(LED_F0r_PIN, bitRead(newOutputState, 1));
    digitalWrite(LED_AUX1_PIN, bitRead(newOutputState, 2));
    digitalWrite(LED_AUX2_PIN, bitRead(newOutputState, 3));
    digitalWrite(LED_AUX3_PIN, bitRead(newOutputState, 4));
    digitalWrite(LED_AUX4_PIN, bitRead(newOutputState, 5));
    digitalWrite(LED_AUX5_PIN, bitRead(newOutputState, 6));
    digitalWrite(LED_AUX6_PIN, bitRead(newOutputState, 7));
    digitalWrite(LED_AUX7_PIN, bitRead(newOutputState, 8));
    digitalWrite(LED_AUX8_PIN, bitRead(newOutputState, 9));
  }
  
  
  if( factoryDefaultCVIndex && dcc.isSetCVReady()){ // handle factory default
    factoryDefaultCVIndex--; // Decrement first as initially it is the size of the array 
    dcc.setCV( factoryDefaultCVs[factoryDefaultCVIndex].CV, factoryDefaultCVs[factoryDefaultCVIndex].Value);
  }
}

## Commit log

2021-02-12 Initial commit
    Initial commit
    [Lokdecoder_TI_altQuartz-B_Cu.gbr, Lokdecoder_TI_altQuartz-B_Mask.gbr, Lokdecoder_TI_altQuartz-B_SilkS.gbr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]
2021-02-14 Trim added,
    Arduino code:
    Comments extended, code cleanup
    - CV15/CV16 locking: local variables (unlockNumber, lockingNumber) created
    - CV27 autstop: : local variable (autoStop) created
    - CV65 kick-off: local variable (kickStart) created
    - CV66/CV95 speed trimming: feature implemented
    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
2021-02-14 PCB images added
2021-02-16 Update dcc_decoder_green.ino
    F_CPU used to calculate PWM
    notifyCVAck fixed
    [dcc_decoder_green.ino]
